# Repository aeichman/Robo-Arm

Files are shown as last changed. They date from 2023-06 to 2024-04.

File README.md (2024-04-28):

# Robo-Arm

6 jointed arm and controller <br />
Project based on https://www.youtube.com/watch?v=wI4Jh-T0Tlo&t=794s with added mirrored controller variation <br />

Reference for 3D prints <br />
Arm - https://www.dropbox.com/s/gp74rmva8efm28f/Arduino%20robot%20arm%20files%20%2B%20step.zip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 (altered parts are in AlteredArm folder, some parts will need to be drilled or dremeled to fit) <br />
Controller - https://github.com/BuildSomeStuff/CompactRoboticArm/blob/main/P.O.T.%20Arm%20Controller%20-%20STL.stl (Updated controller with 6th axis and pen in /Models/Controller) <br />
Claw - In /Models/Claw

# Parts

Arduino Mega <br />
Ramps 1.4 <br />
DRV8825 (x5) <br />
A4988 (for the expansion board and claw) <br />
Nema 17 Bipolar 40mm 45Ncm 2A (x2) <br />
Nema 17 Stepper Motor with 5:1 Planetary Gearbox <br />
Nema 14 Stepper Motor Bipolar 0.5A 7Ncm 0.9deg <br />
Nema 14 Bipolar 1.8deg 5Ncm 0.4A <br />
Nema 8 Bipolar 1.6Ncm/2.3oz.in 1.8deg 28mm 0.2A <br />
608 Bearings (x2) <br />
625 Bearings (x6) <br />
51104 Thrust Bearing <br />
6002-2RS Bearing (x4) <br />
5mm Aluminum Rod <br />
GT2 Belts <br />
10k Ohm Potentiometers (x6) <br />
Variety of M3, M4, and M8 bolts <br />
Micro Limit switches (preferably ones with a wheel) <br/>
Stepper motor expansion board <br />

# Assembly

Setting up stepper motors with the code before assembly is recommended to ensure they are moving in the correct direction. Failure to do so can result in broken parts or torn timing belts. <br/>

Use a piece of patching cloth and super glue to cut and connect GT2 Timing belts to the correct lengths. This can be demonstrated here (https://www.youtube.com/watch?v=T9wjR0HEk3I). <br/>

In each DRV8825 slot, there are 6 micro-stepping pins. On axes X, Z, E0, and E1 using a jumper, connect the m3 pins to enable 1/16 micro-stepping. For the Y-axis jump m2 for 1/8 micro-stepping and on the expansion board, turn on switches 1 & 2 (m1 & m2) for 1/8 micro-stepping.

# DRV8845 & A4988 Vref

Plug driver into the Ramps 1.4 board and connect the power supply. Using a multimeter, touch the positive probe to the potentiometer and the negative to GND. Adjust the multimeter to the Vref calculated by the following equations. <br/>

C = Current Limit of Steppper Motor <br/>
Rs = Current sensor resistor <br/>

DRV8845: Vref = C / 2 <br/>
A4988: Vref = C _ 8 _ Rs <br/>

# Code

Test each stepper motor driver with StepperSetup.cc to ensure proper direction <br/>

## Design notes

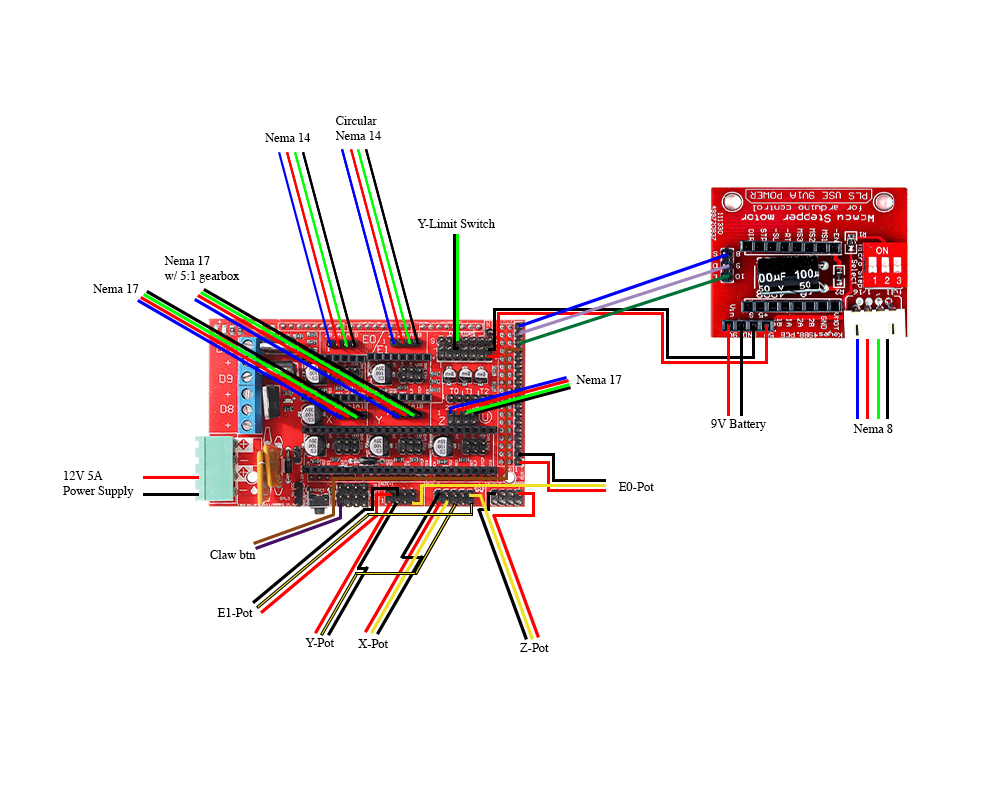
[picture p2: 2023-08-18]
Schematics/Robo-Arm-Schematic.png

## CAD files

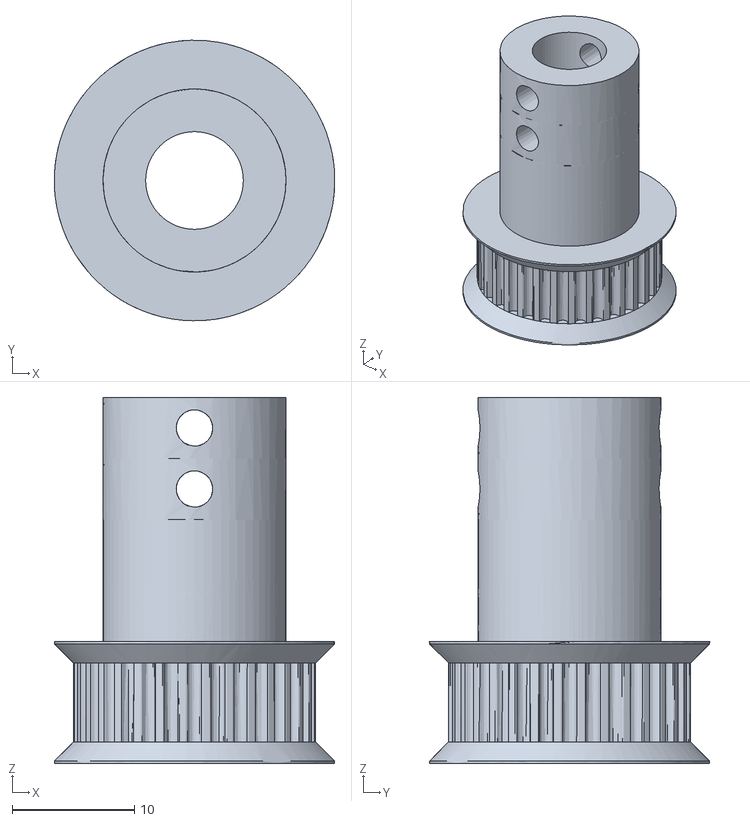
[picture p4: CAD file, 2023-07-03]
Models/AlteredArm/32TLongGear.stl
23.0 x 23.0 x 30.0

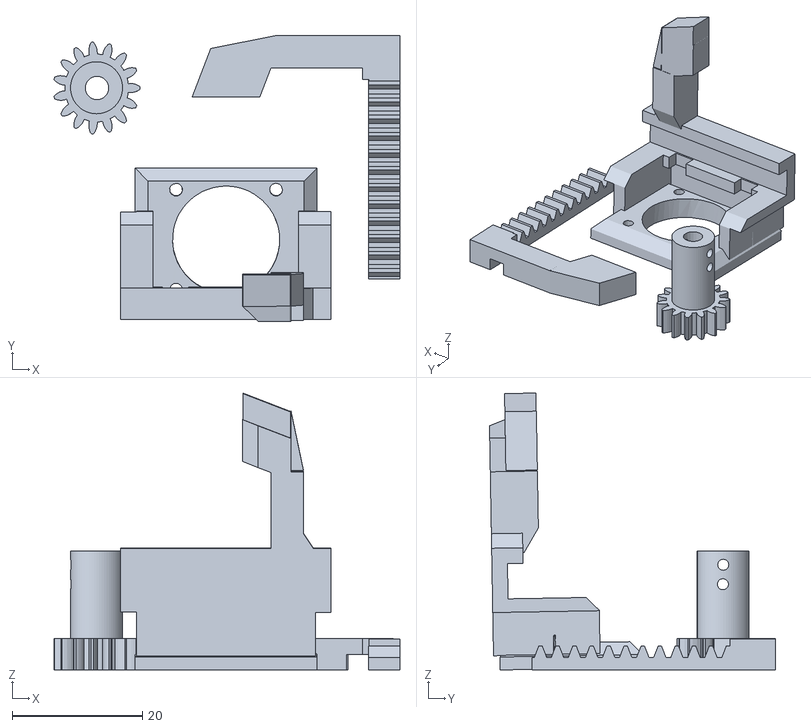
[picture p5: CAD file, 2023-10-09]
Models/Claw/Claw v4.stl
53.2 x 44.0 x 42.6

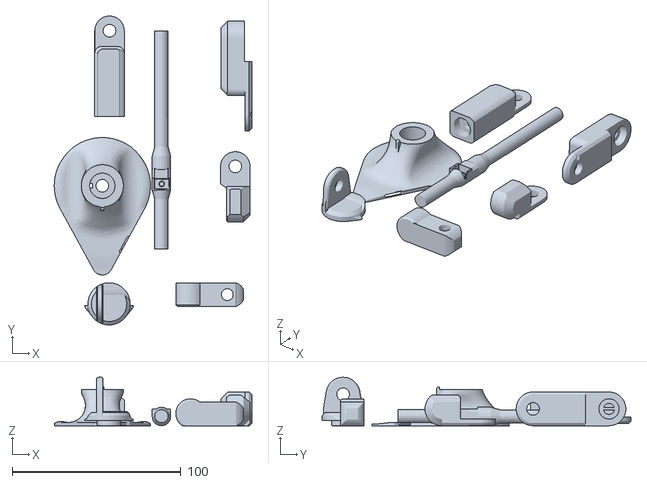
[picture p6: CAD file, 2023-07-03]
Models/Controller/ControllerJoints2.0.stl
117.0 x 183.0 x 28.8

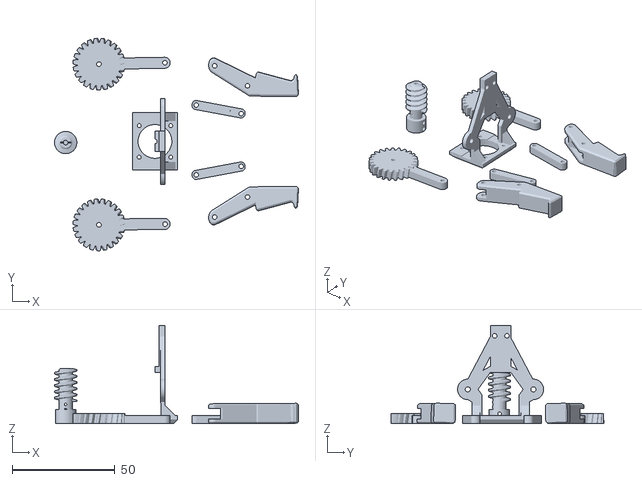
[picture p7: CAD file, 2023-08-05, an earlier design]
Models/Claw/Claw_v3.stl
119.0 x 103.7 x 48.0

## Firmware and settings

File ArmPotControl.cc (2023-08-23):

// Arduino Code
#include <AccelStepper.h>
#include <Bounce2.h>

#define X_STEP_PIN 54
#define X_DIR_PIN 55
#define X_ENABLE_PIN 38

#define Y_STEP_PIN 60
#define Y_DIR_PIN 61
#define Y_ENABLE_PIN 56
#define Y_LIMIT_PIN 14

#define Z_STEP_PIN 46
#define Z_DIR_PIN 48
#define Z_ENABLE_PIN 62

#define E1_STEP_PIN 26
#define E1_DIR_PIN 28
#define E1_ENABLE_PIN 24

#define E2_STEP_PIN 36
#define E2_DIR_PIN 34
#define E2_ENABLE_PIN 30

#define C_STEP_PIN 16
#define C_DIR_PIN 17
#define C_ENABLE_PIN 23

#define X_POT_PIN A5
#define Y_POT_PIN A10
#define Z_POT_PIN A11
#define E1_POT_PIN A12
#define E2_POT_PIN A4

#define BUTTON_PIN 25
#define Y_LIMIT_PIN 14

// Can vary depending on microstepping settings
#define STEPS_PER_REV_X 6400
#define STEPS_PER_REV_Y 15000
#define STEPS_PER_REV_Z 6400
#define STEPS_PER_REV_E1 6400
#define STEPS_PER_REV_E2 6400
#define STEPS_PER_REV_C 1200

AccelStepper stepperX(AccelStepper::DRIVER, X_STEP_PIN, X_DIR_PIN);
AccelStepper stepperY(AccelStepper::DRIVER, Y_STEP_PIN, Y_DIR_PIN);
AccelStepper stepperZ(AccelStepper::DRIVER, Z_STEP_PIN, Z_DIR_PIN);
AccelStepper stepperE1(AccelStepper::DRIVER, E1_STEP_PIN, E1_DIR_PIN);
AccelStepper stepperE2(AccelStepper::DRIVER, E2_STEP_PIN, E2_DIR_PIN);
AccelStepper stepperC(AccelStepper::DRIVER, C_STEP_PIN, C_DIR_PIN);

enum ClawState
{
    STOPPED,
    COUNTER_CLOCKWISE,
    STOPPING,
    CLOCKWISE
};

ClawState currentClawState = STOPPED;

Bounce button = Bounce();
bool motorRunning = false;
bool lastButtonState = HIGH;

int prevXPotValue = 0;
int prevYPotValue = 0;
int prevZPotValue = 0;
int prevE1PotValue = 0;
int prevE2PotValue = 0;

void mySetup()
{

    stepperX.setMaxSpeed(8000);     // Maximum speed in steps per second
    stepperX.setAcceleration(4000); // Acceleration in steps per second^2
    stepperY.setMaxSpeed(35000);
    stepperY.setAcceleration(20000);
    stepperZ.setMaxSpeed(4000);
    stepperZ.setAcceleration(1000);
    stepperE1.setMaxSpeed(6000);
    stepperE1.setAcceleration(3000);
    stepperE2.setMaxSpeed(3000);
    stepperE2.setAcceleration(1000);
    stepperC.setMaxSpeed(2000);
    stepperC.setAcceleration(2500);

    pinMode(X_ENABLE_PIN, OUTPUT);
    digitalWrite(X_ENABLE_PIN, LOW);
    pinMode(Y_ENABLE_PIN, OUTPUT);
    digitalWrite(Y_ENABLE_PIN, LOW);
    pinMode(Z_ENABLE_PIN, OUTPUT);
    digitalWrite(Z_ENABLE_PIN, LOW);
    pinMode(E1_ENABLE_PIN, OUTPUT);
    digitalWrite(E1_ENABLE_PIN, LOW);
    pinMode(E2_ENABLE_PIN, OUTPUT);
    digitalWrite(E2_ENABLE_PIN, LOW);
    pinMode(C_ENABLE_PIN, OUTPUT);
    digitalWrite(C_ENABLE_PIN, LOW);
    pinMode(BUTTON_PIN, INPUT_PULLUP);
    pinMode(Y_LIMIT_PIN, INPUT_PULLUP);

    // Set the initial positions of the stepper motors to 0 change for homing
    stepperX.setCurrentPosition(0);
    stepperY.setCurrentPosition(0);
    stepperZ.setCurrentPosition(0);
    stepperE1.setCurrentPosition(0);
    stepperE2.setCurrentPosition(0);
    stepperC.setCurrentPosition(0);

    button.attach(BUTTON_PIN);
    button.interval(5);
}

void setup()
{
    mySetup();
}

void loop()
{
    int xPotValue = analogRead(X_POT_PIN);
    int yPotValue = analogRead(Y_POT_PIN);
    int zPotValue = analogRead(Z_POT_PIN);
    int e1PotValue = analogRead(E1_POT_PIN);
    int e2PotValue = analogRead(E2_POT_PIN);

    if (xPotValue != prevXPotValue)
    {
        int xTargetPosition = map(xPotValue, 0, 1023, 0, STEPS_PER_REV_X);
        stepperX.moveTo(xTargetPosition);
        prevXPotValue = xPotValue;
    }

    if (yPotValue != prevYPotValue)
    {
        int yTargetPosition = map(yPotValue, 0, 1023, 0, STEPS_PER_REV_Y);
        stepperY.moveTo(yTargetPosition);
        prevYPotValue = yPotValue;
    }

    if (zPotValue != prevZPotValue)
    {
        int zTargetPosition = map(zPotValue, 0, 1023, 0, STEPS_PER_REV_Z);
        stepperZ.moveTo(zTargetPosition);
        prevZPotValue = zPotValue;
    }

    if (e1PotValue != prevE1PotValue)
    {
        int e1TargetPosition = map(e1PotValue, 0, 1023, 0, STEPS_PER_REV_E1);
        stepperE1.moveTo(e1TargetPosition);
        prevE1PotValue = e1PotValue;
    }

    if (e2PotValue != prevE2PotValue)
    {
        int e2TargetPosition = map(e2PotValue, 0, 1023, 0, STEPS_PER_REV_E2);
        stepperE2.moveTo(e2TargetPosition);
        prevE2PotValue = e2PotValue;
    }

    // Run the stepper movements
    stepperX.run();
    stepperY.run();
    stepperZ.run();
    stepperE1.run();
    stepperE2.run();

    // int xTargetPosition = map(xPotValue, 0, 1023, 0, STEPS_PER_REV_X);
    // int yTargetPosition = map(yPotValue, 0, 1023, 0, STEPS_PER_REV_Y);
    // int zTargetPosition = map(zPotValue, 0, 1023, 0, STEPS_PER_REV_Z);
    // int e1TargetPosition = map(e1PotValue, 0, 1023, 0, STEPS_PER_REV_E1);
    // int e2TargetPosition = map(e2PotValue, 0, 1023, 0, STEPS_PER_REV_E2);

    // stepperX.moveTo(xTargetPosition);
    // stepperY.moveTo(yTargetPosition);
    // stepperZ.moveTo(zTargetPosition);
    // stepperE1.moveTo(e1TargetPosition);
    // stepperE2.moveTo(e2TargetPosition);

    // stepperX.run();
    // stepperY.run();
    // stepperZ.run();
    // stepperE1.run();
    // stepperE2.run();

    button.update();

    if (button.fell())
    {
        switch (currentClawState)
        {
        case STOPPED:
            // Motor starts running counter-clockwise on first click
            currentClawState = COUNTER_CLOCKWISE;
            stepperC.setSpeed(-500);
            stepperC.runSpeed();
            break;
        case COUNTER_CLOCKWISE:
            // Motor stops on second click
            currentClawState = STOPPING;
            stepperC.stop();
            break;
        case STOPPING:
            // Motor starts running clockwise on third click
            currentClawState = CLOCKWISE;
            stepperC.setSpeed(500);
            stepperC.runSpeed();
            break;
        case CLOCKWISE:
            // Motor stops on fourth click
            currentClawState = STOPPED;
            stepperC.stop();
            break;
        }
    }

    if (currentClawState == COUNTER_CLOCKWISE || currentClawState == CLOCKWISE)
    {
        stepperC.runSpeed();
    }
}

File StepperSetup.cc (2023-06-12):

// Note: This is for Arduino Programming, a simplified version of C++

byte directionPin = 5;
byte stepPin = 2;
byte enablePin = 8; // must enable steppers.

int numberOfSteps = 200;     // 200 for Nema17
int pulseWidthMicros = 50;   // microseconds
int millisbetweenSteps = 30; // time between steps in milliseconds

void setup()
{

    Serial.begin(115200);
    Serial.println("Starting StepperTest");

    delay(2000);

    pinMode(directionPin, OUTPUT);
    pinMode(stepPin, OUTPUT);
    pinMode(enablePin, OUTPUT);
    digitalWrite(enablePin, LOW);

    digitalWrite(directionPin, HIGH);
    for (int n = 0; n < numberOfSteps; n++)
    {
        digitalWrite(stepPin, HIGH);
        digitalWrite(stepPin, LOW);

        delay(millisbetweenSteps);
    }

    delay(2000);

    digitalWrite(directionPin, LOW);
    for (int n = 0; n < numberOfSteps; n++)
    {
        digitalWrite(stepPin, HIGH);
        digitalWrite(stepPin, LOW);

        delay(millisbetweenSteps);
    }
}

void loop()
{
}

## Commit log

2023-05-15 Create StepperSetup.cc
    Program to test stepper motor
2023-05-16 Base Models
    [BaseWall_2_v2.STL, Basewall cover v2.STL, Motor1 spacer.STL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]
2023-05-17 Models baseplate
    [Baseplate.STL, Bottom Tube.STL, Bottom support.STL]
2023-06-12 Adding Arduino Mega capabilities
    Able to use the ramps 1.4 board to control nema 17 with pot
    [Bottom support.STL]
2023-07-03 Adding models and update ReadMe
    [32TLongGear.stl, BaseWall_2_v2.STL, Baseplate.STL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]
2023-08-05 Adding final controls and claw
    [Claw_v3.stl]
2023-08-16 Adding new claw model
    [Claw v4.stl]
2023-08-18 Code updates and schematics
2023-09-15 Schematics, Stepper settings, and README
2023-10-09 Update Claw v4.stl
    [Claw v4.stl]
